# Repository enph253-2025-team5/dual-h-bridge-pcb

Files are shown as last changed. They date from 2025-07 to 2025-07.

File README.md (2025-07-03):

# Dual H-Bridge PCB

Dual h-bridge design with a PWM signal and direction bit for controlling two motors.

Similar to Greg Reid's 2025 h-bridge design, without relying on tripping the overcurrent protection. Instead, this design duplicates the incoming PWM signal, sends one to each of the low side h-bridge MOSFETs, then pulls the gate with the enhanced high side MOSFET low (avoiding shoot-through). 

Based on many factors (motor inertia, gate driver response, optocoupler distortion) the PWM frequency should be limited on the order of 100 Hz.
Intended motor battery configuration of 4S.

**BOM, Schematic, and PCB drawings in the latest release.**

## Images
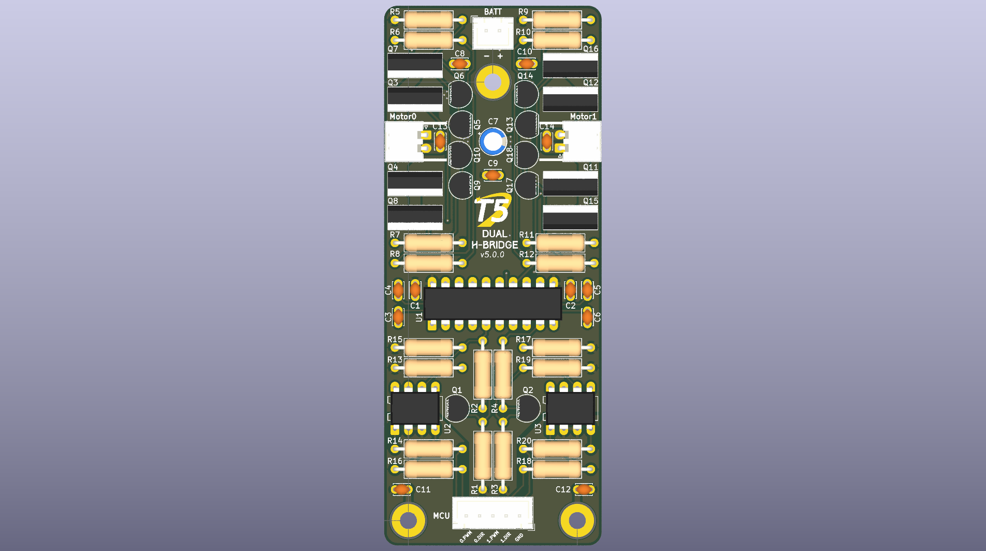
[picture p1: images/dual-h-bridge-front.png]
dual-h-bridge-front

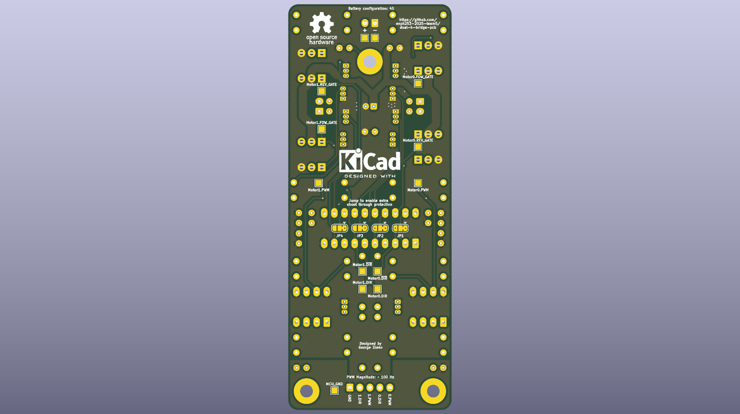
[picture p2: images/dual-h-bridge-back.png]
dual-h-bridge-back

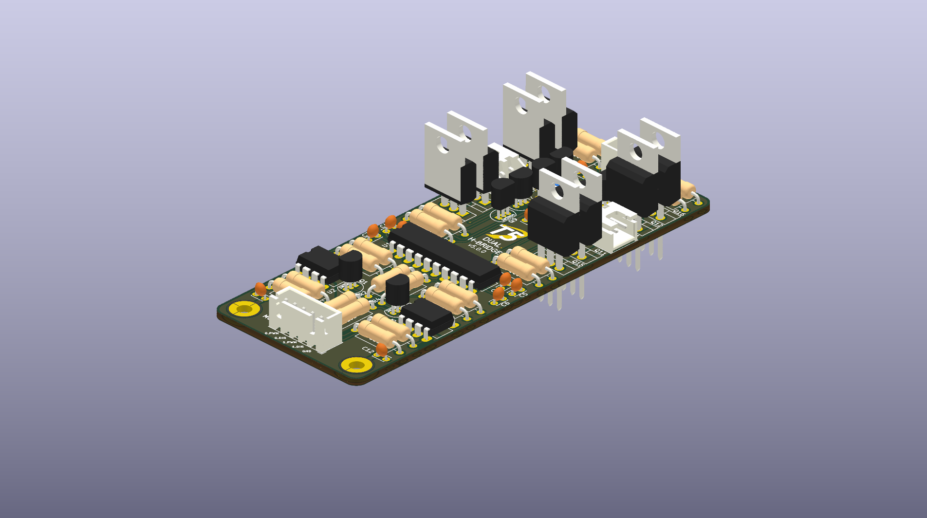
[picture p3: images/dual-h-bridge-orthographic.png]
dual-h-bridge-orthographic


Designed by George Sleen.

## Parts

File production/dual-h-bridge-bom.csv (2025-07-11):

Value | Qty | Reference | Footprint
LT1161 | 1 | U1 | Package_DIP:DIP-20_W7.62mm_LongPads
MCT6 | 2 | U2,U3 | Package_DIP:DIP-8_W7.62mm_LongPads
Motor0 | 1 | J1 | GS_Connectors:JST_XH_S2B-XH-A-1_1x02_P2.50mm_Horizontal
Motor1 | 1 | J3 | GS_Connectors:JST_XH_S2B-XH-A-1_1x02_P2.50mm_Horizontal
BATT | 1 | J4 | Connector_JST:JST_XH_B2B-XH-A_1x02_P2.50mm_Vertical
MCU | 1 | J2 | Connector_JST:JST_XH_B5B-XH-A_1x05_P2.50mm_Vertical
VN2222L | 4 | Q5,Q10,Q13,Q18 | Package_TO_SOT_THT:TO-92_Inline
IRFZ44 | 8 | Q3,Q4,Q7,Q8,Q11,Q12,Q15,Q16 | Package_TO_SOT_THT:TO-220-3_Vertical
2N3904 | 6 | Q1,Q2,Q6,Q9,Q14,Q17 | Package_TO_SOT_THT:TO-92_Inline
47uF | 1 | C7 | Capacitor_THT:CP_Radial_D5.0mm_P2.00mm
10k | 12 | R1,R2,R3,R4,R5,R7,R9,R11,R13,R15,R17,R19 | Resistor_THT:R_Axial_DIN0309_L9.0mm_D3.2mm_P12.70mm_Horizontal
100k | 4 | R6,R8,R10,R12 | Resistor_THT:R_Axial_DIN0309_L9.0mm_D3.2mm_P12.70mm_Horizontal
330R | 4 | R14,R16,R18,R20 | Resistor_THT:R_Axial_DIN0309_L9.0mm_D3.2mm_P12.70mm_Horizontal
100nF | 9 | C1,C2,C8,C9,C10,C11,C12,C13,C14 | Capacitor_THT:C_Disc_D3.0mm_W2.0mm_P2.50mm
10nF | 4 | C3,C4,C5,C6 | Capacitor_THT:C_Disc_D3.0mm_W2.0mm_P2.50mm

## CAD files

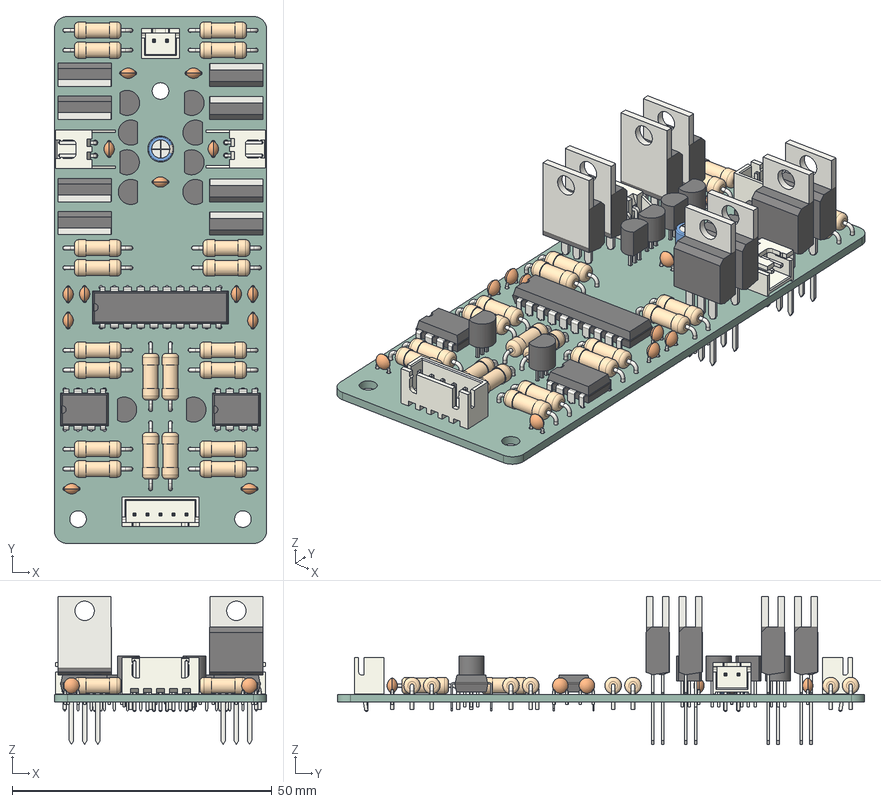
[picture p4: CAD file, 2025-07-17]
3d-model/dual-h-bridge.step
40.9 x 101.5 x 28.5 mm
TO-92_Inline x 10
R_Axial_DIN0309_L9.0mm_D3.2mm_P12.70mm_Horizontal x 20
C_Disc_D3.0mm_W2.0mm_P2.50mm x 13
CP_Radial_D5.0mm_P2.00mm
TO-220-3_Vertical x 8
JST_XH_B2B-XH-A_1x02_P2.50mm_Vertical
JST_XH_S2B-XH-A-1_1x02_P2.50mm_Horizontal x 2
DIP-8_W7.62mm x 2
JST_XH_B5B-XH-A_1x05_P2.50mm_Vertical
DIP-20_W7.62mm
dual-h-bridge_PCB

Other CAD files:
drawings/dual-h-bridge.step
prod/motor-controller.step
drawings/.step

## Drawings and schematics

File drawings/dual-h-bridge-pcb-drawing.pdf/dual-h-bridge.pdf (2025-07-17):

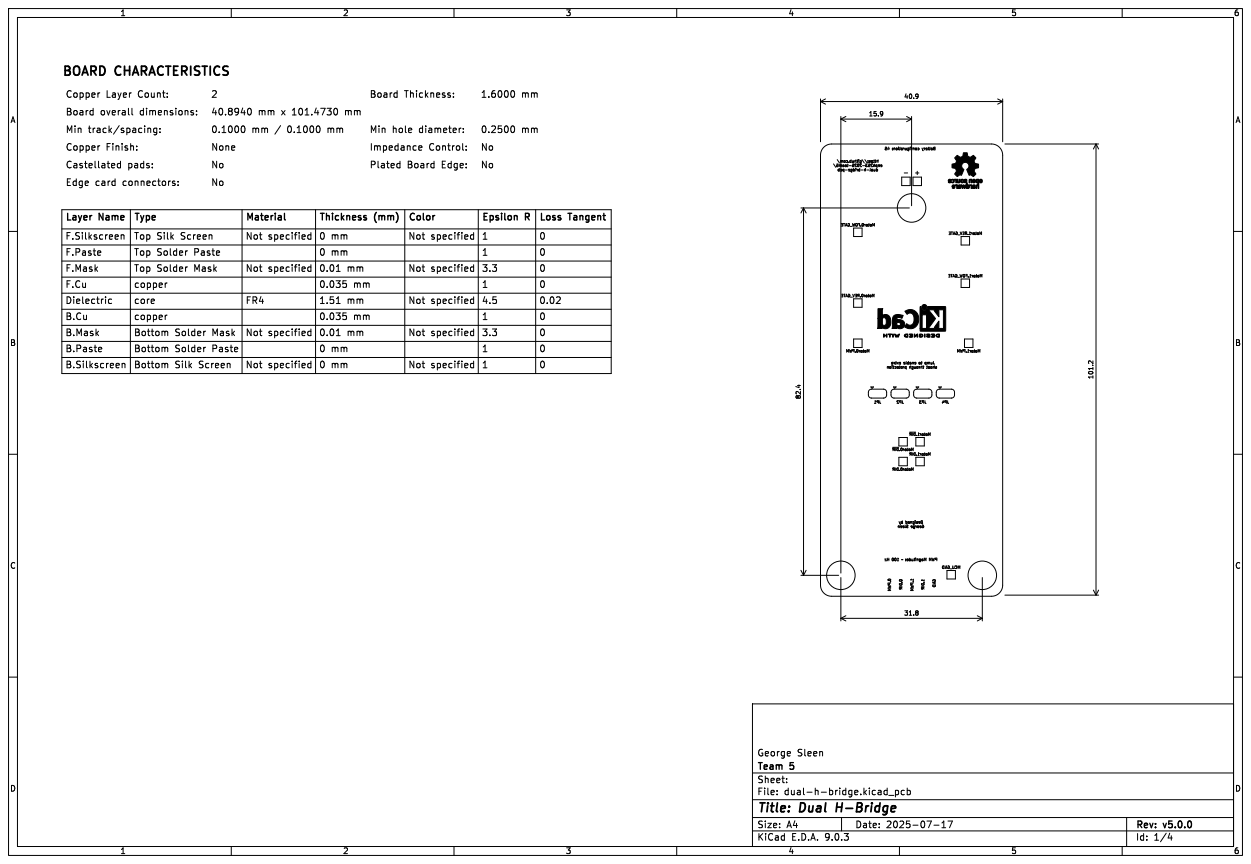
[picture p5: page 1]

Layer Name Copper Finish: | Thickness (mm) | Not specified | 3.3 Plated Board Edge: 1.51 mm | 0

F.Silkscreen F.Paste | | | | Material | 0 mm | Not specified | 4.5 Not specified | Loss Tangent Not specified 0

Top Silk Screen | | 0 mm | | 1

0.035 mm | | | 0 Bottom Silk Screen 0

core B.Silkscreen | | 0.035 mm

0 Not specified

Bottom Solder Paste

File: dual-h-bridge.kicad_pcb Sheet: Team 5 George Sleen

Id: 1/4 Title: Dual H-Bridge

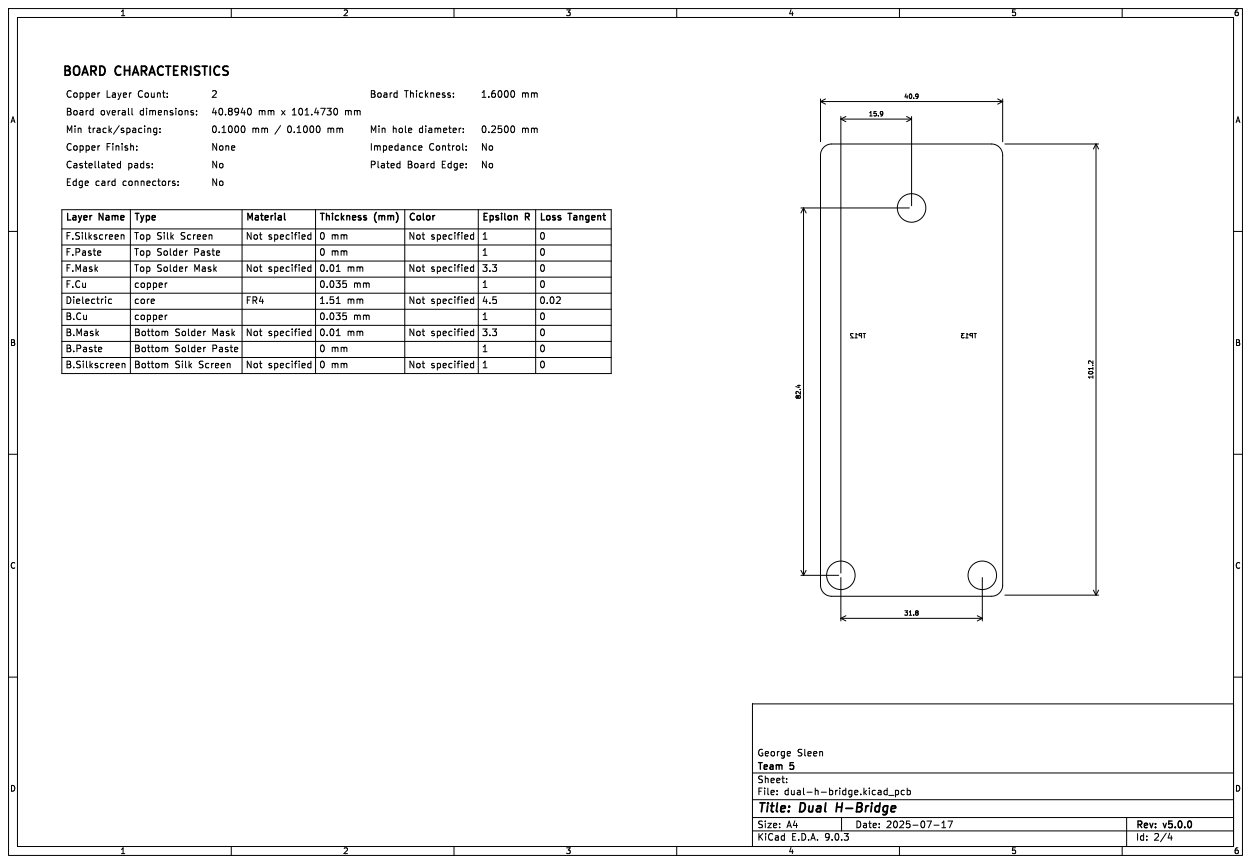
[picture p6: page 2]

Layer Name Copper Finish: | Thickness (mm) mm | Not specified Board Edge: 1.51 | 3.3 Plated | 0

F.Silkscreen F.Paste | | | | Material | 0 mm | Not specified | | Loss Tangent Not specified 0

Top Silk Screen | | 0 mm | | | 1

Screen | | 0.035 mm | | | 0 Bottom Silk 0

core B.Silkscreen | | 0.035 mm

0 Not specified

File: dual-h-bridge.kicad_pcb Sheet: Team 5 George Sleen

Id: 2/4 Title: Dual H-Bridge

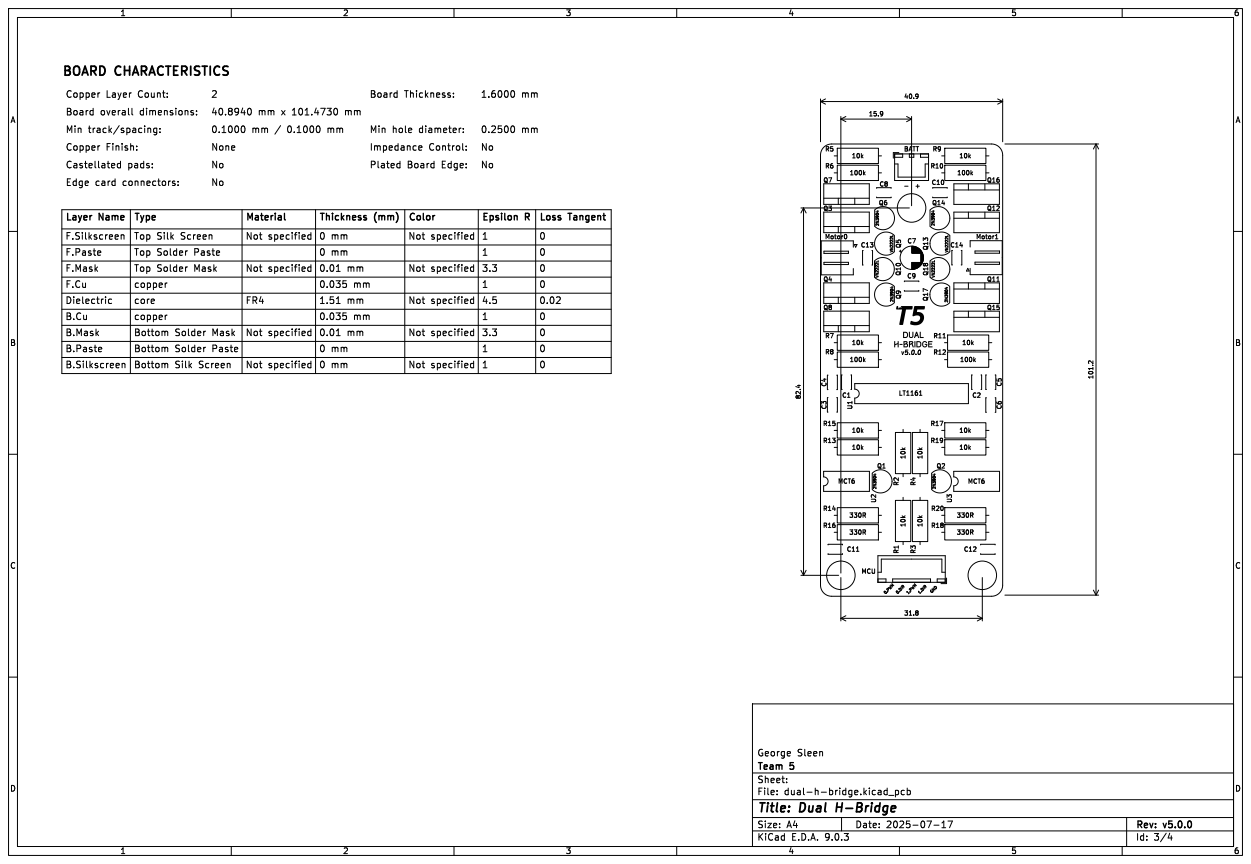
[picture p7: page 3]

Layer Name Copper Finish: | | Thickness (mm) | Not specified | 3.3 Plated Board Edge: 1.51 mm Epsilon R | 0

F.Silkscreen F.Paste | | | | Material | 0 mm | Not specified | 4.5 Not specified | Loss Tangent Not specified 0
0 mm 0.035 mm | Not specified F.Mask | | 0 Bottom Silk Screen 0

Top Silk Screen | 0 mm | | 1

core B.Silkscreen | | | | 0.035 mm

FR4 | | | | 0.02
0.01 mm | | | 0 Not specified

Bottom Solder Paste | | | | | | 1

File: dual-h-bridge.kicad_pcb Sheet: Team 5 George Sleen

Id: 3/4 Title: Dual H-Bridge

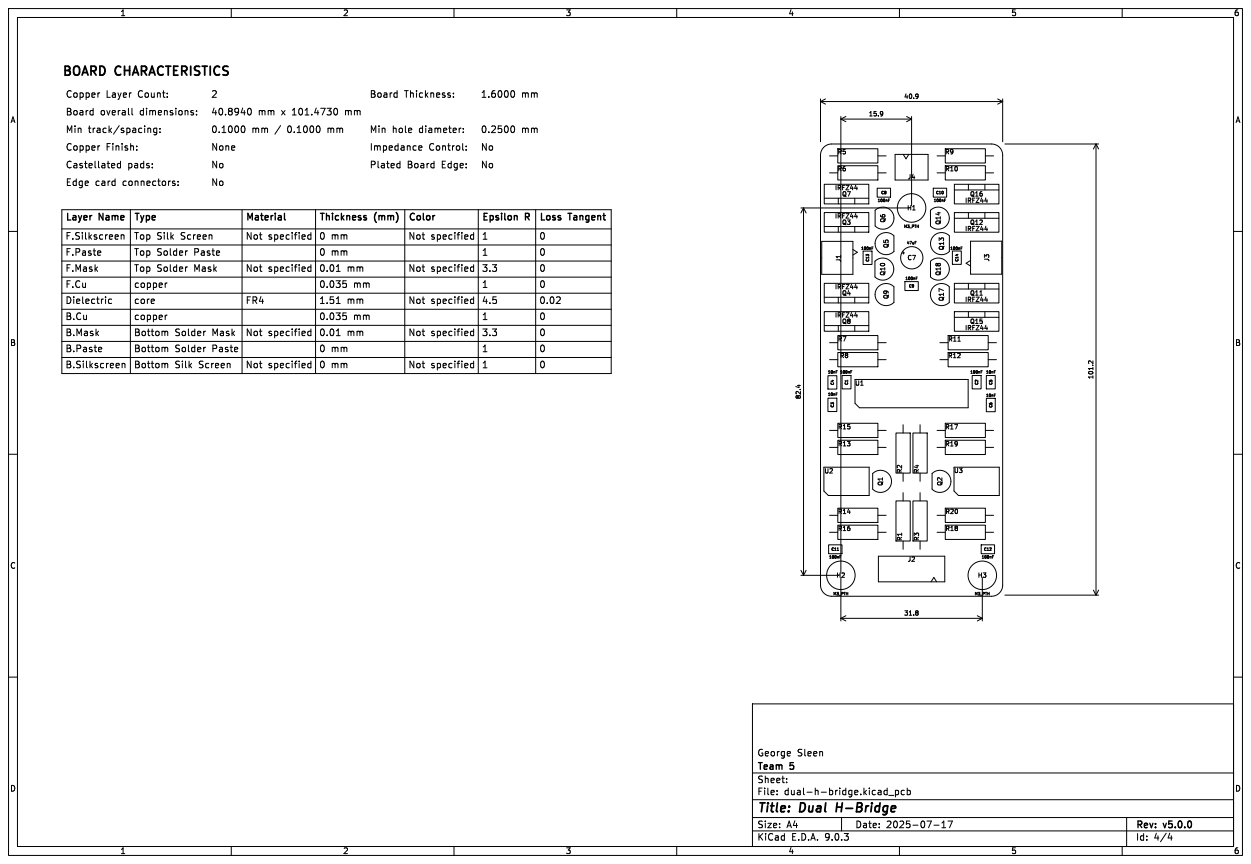
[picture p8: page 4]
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

Top Silk Screen | 0 mm | | 1

0.035 mm | | | 0 Bottom Silk Screen 0

0 Not specified

Bottom Solder Paste

Id: 4/4 Title: Dual H-Bridge

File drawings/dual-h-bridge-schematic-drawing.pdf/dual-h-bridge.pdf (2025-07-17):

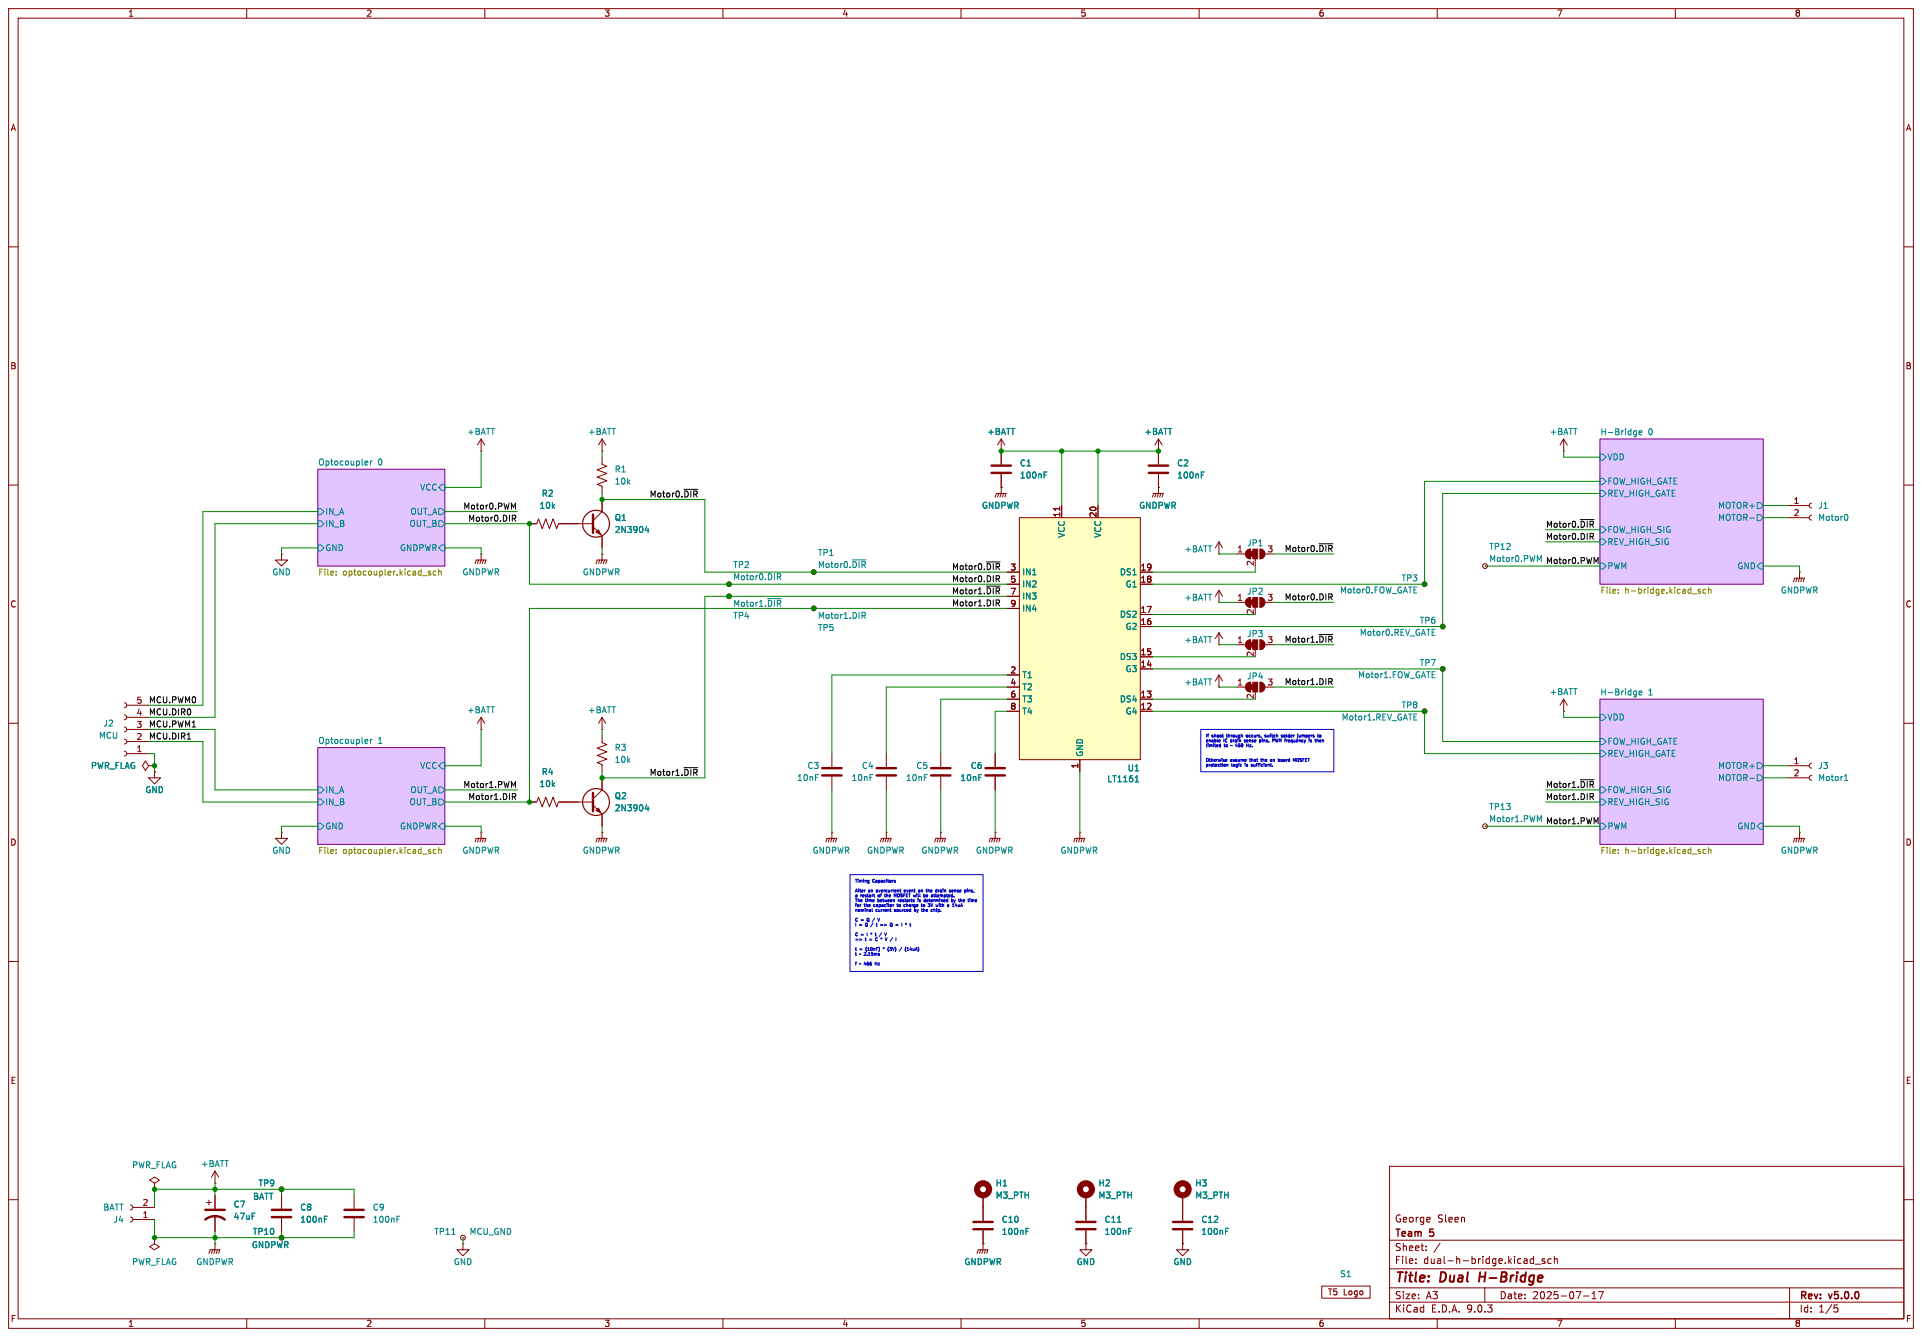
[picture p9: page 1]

Id: 1/5 Title: Dual H-Bridge

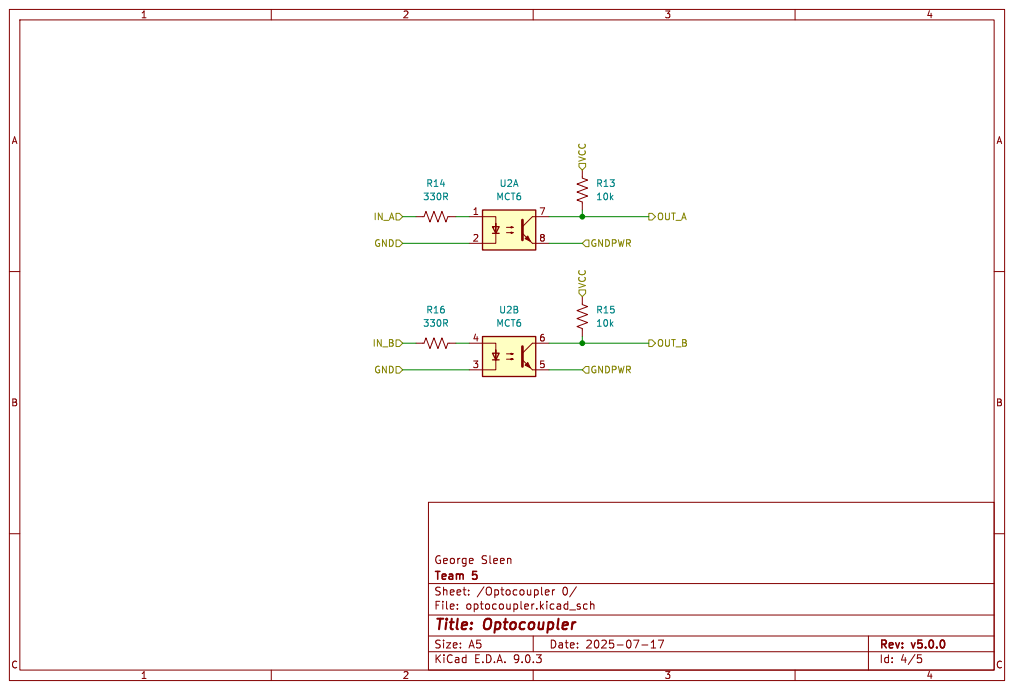
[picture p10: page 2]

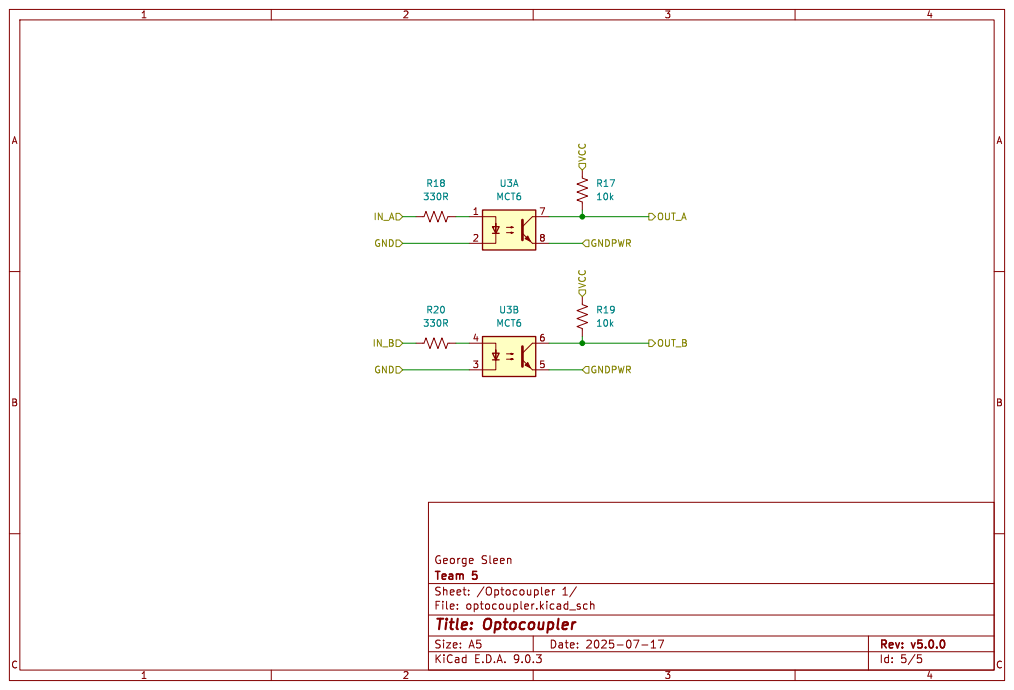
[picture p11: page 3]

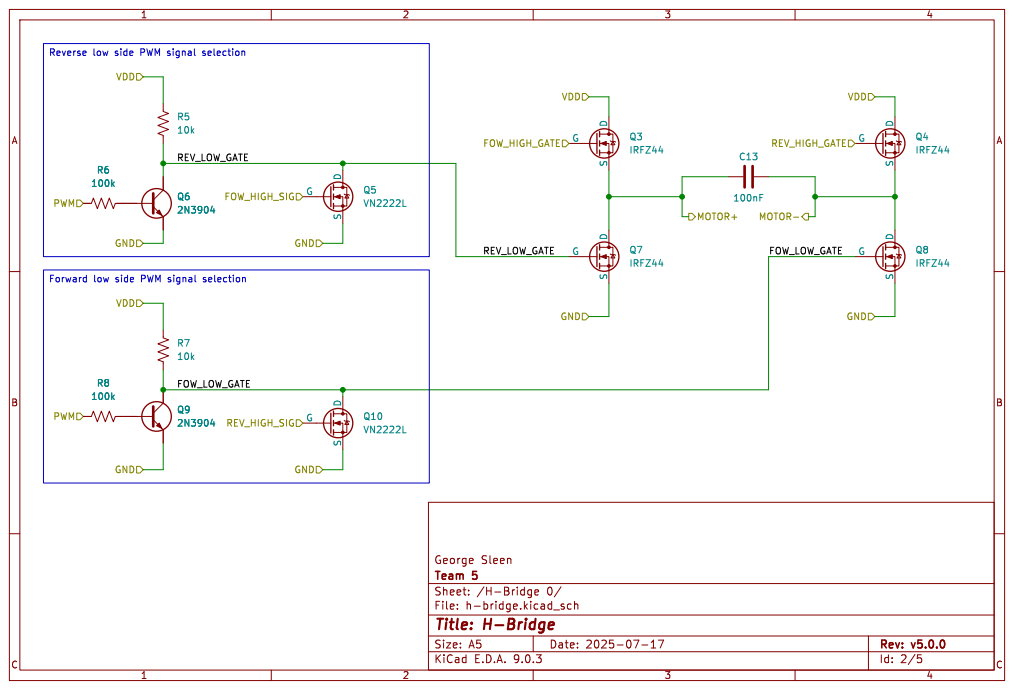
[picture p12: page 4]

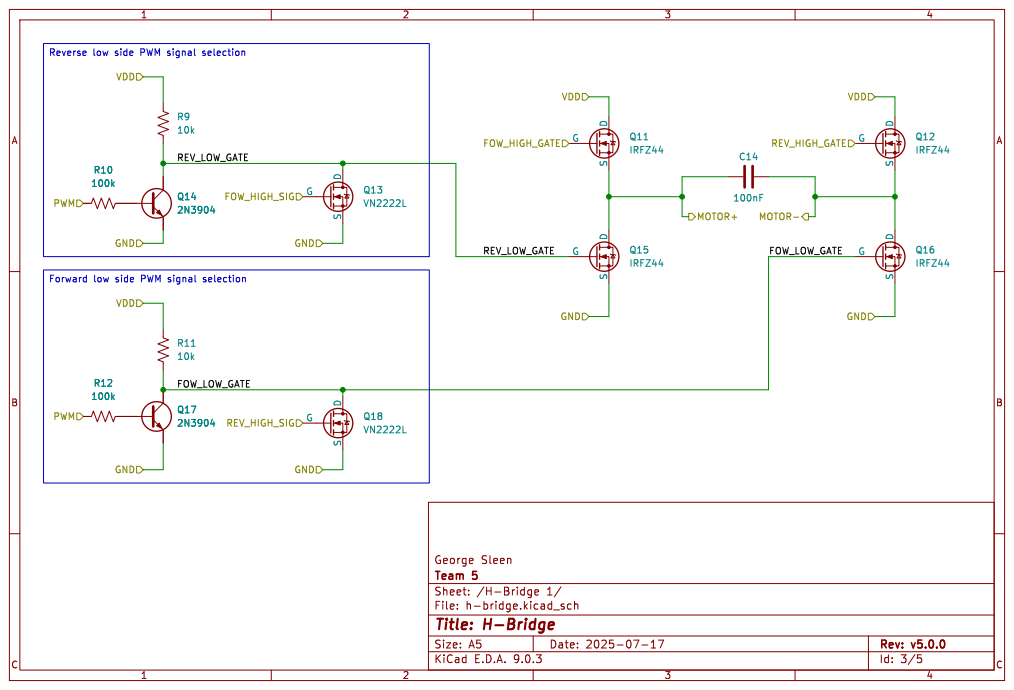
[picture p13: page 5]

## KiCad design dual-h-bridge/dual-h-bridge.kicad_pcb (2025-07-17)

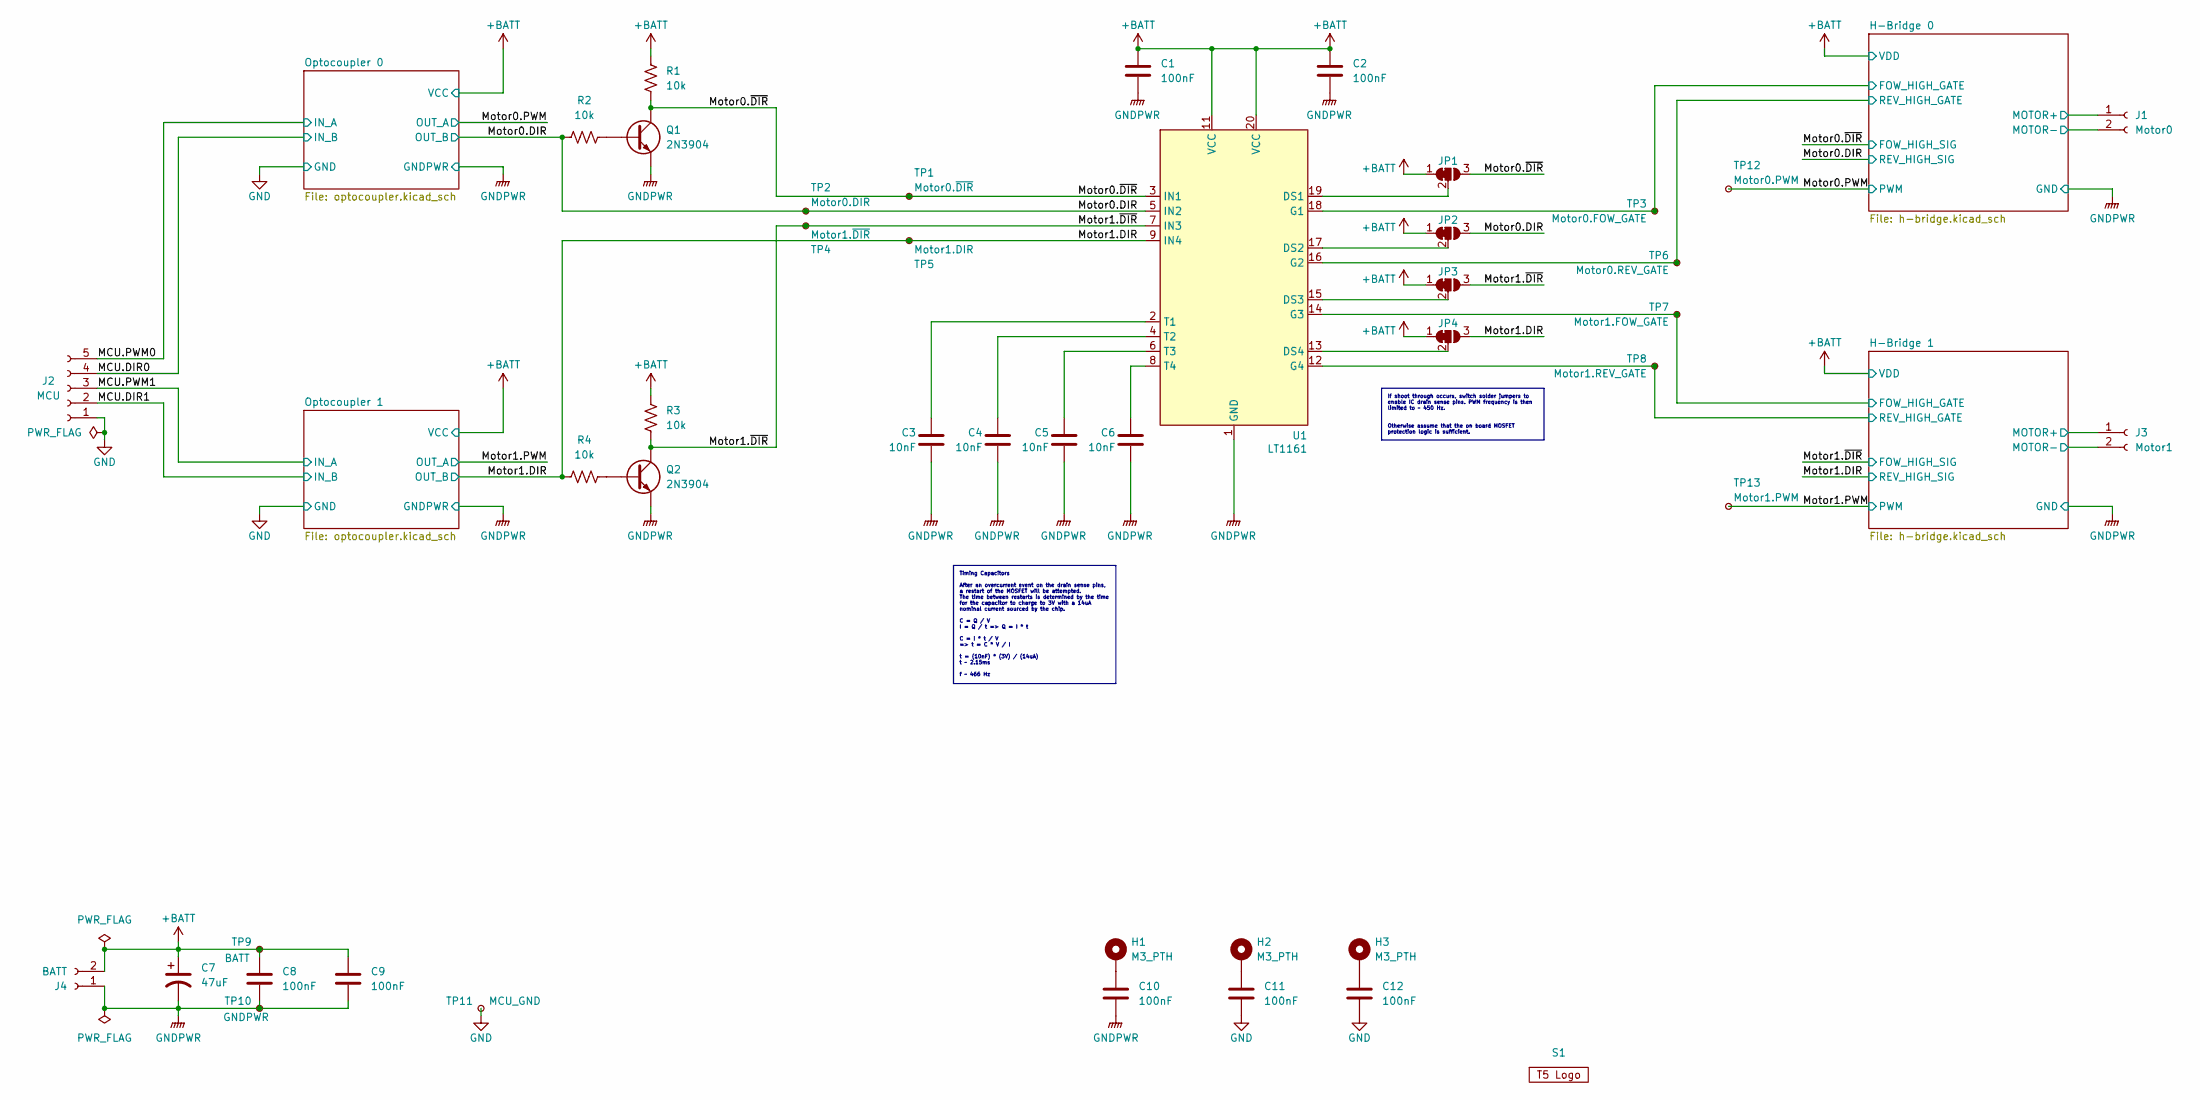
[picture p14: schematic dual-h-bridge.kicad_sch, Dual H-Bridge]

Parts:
C1, C2, C8, C9, C10, C11, C12: 100nF; C_Disc_D3.0mm_W2.0mm_P2.50mm
C3, C4, C5, C6: 10nF; C_Disc_D3.0mm_W2.0mm_P2.50mm
C7: 47uF; CP_Radial_D5.0mm_P2.00mm
H1, H2, H3: M3_PTH; MountingHole_3.2mm_M3_Pad
J1: Motor0; JST_XH_S2B-XH-A-1_1x02_P2.50mm_Horizontal
J2: MCU; JST_XH_B5B-XH-A_1x05_P2.50mm_Vertical
J3: Motor1; JST_XH_S2B-XH-A-1_1x02_P2.50mm_Horizontal
J4: BATT; JST_XH_B2B-XH-A_1x02_P2.50mm_Vertical
JP1: Motor0_FOW; SolderJumper-3_P1.3mm_Bridged12_RoundedPad1.0x1.5mm
JP2: MOTOR0_REV; SolderJumper-3_P1.3mm_Bridged12_RoundedPad1.0x1.5mm
JP3: MOTOR1_FOW; SolderJumper-3_P1.3mm_Bridged12_RoundedPad1.0x1.5mm
JP4: MOTOR1_REV; SolderJumper-3_P1.3mm_Bridged12_RoundedPad1.0x1.5mm
Q1, Q2: 2N3904; TO-92_Inline
R1, R2, R3, R4: 10k; R_Axial_DIN0309_L9.0mm_D3.2mm_P12.70mm_Horizontal
S1: Logo; ENPH253_Logo_Small
TP1: Motor0.~{DIR}; TestPoint_Pad_1.5x1.5mm
TP2: Motor0.DIR; TestPoint_Pad_1.5x1.5mm
TP3: Motor0.FOW_GATE; TestPoint_Pad_1.5x1.5mm
TP4: Motor1.~{DIR}; TestPoint_Pad_1.5x1.5mm
TP5: Motor1.DIR; TestPoint_Pad_1.5x1.5mm
TP6: Motor0.REV_GATE; TestPoint_Pad_1.5x1.5mm
TP7: Motor1.FOW_GATE; TestPoint_Pad_1.5x1.5mm
TP8: Motor1.REV_GATE; TestPoint_Pad_1.5x1.5mm
TP9: BATT; TestPoint_Pad_1.5x1.5mm
TP10: GNDPWR; TestPoint_Pad_1.5x1.5mm
TP11: MCU_GND; TestPoint_Pad_1.5x1.5mm
TP12: Motor0.PWM; TestPoint_Pad_1.5x1.5mm
TP13: Motor1.PWM; TestPoint_Pad_1.5x1.5mm
U1: LT1161; DIP-20_W7.62mm_LongPads

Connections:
+BATT: C1.1, C2.1, C7.1, C8.1, C9.1, J4.2, JP1.1 (A), JP2.1 (A), JP3.1 (A), JP4.1 (A), R1.1, R3.1, TP9.1, U1.11 (VCC), U1.20 (VCC); also elsewhere on the board
/H-Bridge 0/FOW_HIGH_GATE: TP3.1, U1.18 (G1); also elsewhere on the board
/H-Bridge 0/MOTOR+: J1.1; also elsewhere on the board
/H-Bridge 0/MOTOR-: J1.2; also elsewhere on the board
/H-Bridge 0/REV_HIGH_GATE: TP6.1, U1.16 (G2); also elsewhere on the board
/H-Bridge 1/FOW_HIGH_GATE: TP7.1, U1.14 (G3); also elsewhere on the board
/H-Bridge 1/MOTOR+: J3.1; also elsewhere on the board
/H-Bridge 1/MOTOR-: J3.2; also elsewhere on the board
/H-Bridge 1/REV_HIGH_GATE: TP8.1, U1.12 (G4); also elsewhere on the board
/MCU.DIR0: J2.4; also elsewhere on the board
/MCU.DIR1: J2.2; also elsewhere on the board
/MCU.PWM0: J2.5; also elsewhere on the board
/MCU.PWM1: J2.3; also elsewhere on the board
/Motor0.DIR: JP2.3 (B), R2.1, TP2.1, U1.5 (IN2); also elsewhere on the board
/Motor0.PWM: TP12.1; also elsewhere on the board
/Motor0.~DIR: JP1.3 (B), Q1.3 (C), R1.2, TP1.1, U1.3 (IN1); also elsewhere on the board
/Motor1.DIR: JP4.3 (B), R4.1, TP5.1, U1.9 (IN4); also elsewhere on the board
/Motor1.PWM: TP13.1; also elsewhere on the board
/Motor1.~DIR: JP3.3 (B), Q2.3 (C), R3.2, TP4.1, U1.7 (IN3); also elsewhere on the board
GND: C11.2, C12.2, J2.1, TP11.1; also elsewhere on the board
GNDPWR: C1.2, C2.2, C3.2, C4.2, C5.2, C6.2, C7.2, C8.2, C9.2, C10.2, J4.1, Q1.1 (E), Q2.1 (E), TP10.1, U1.1 (GND), U1.10 (GND); also elsewhere on the board
unnamed: C10.1, H1.1
unnamed: C11.1, H2.1
unnamed: C12.1, H3.1
unnamed: JP1.2 (C), U1.19 (DS1)
unnamed: JP2.2 (C), U1.17 (DS2)
unnamed: JP3.2 (C), U1.15 (DS3)
unnamed: JP4.2 (C), U1.13 (DS4)
unnamed: Q1.2 (B), R2.2
unnamed: Q2.2 (B), R4.2
unnamed: C3.1, U1.2 (T1)
unnamed: C4.1, U1.4 (T2)
unnamed: C5.1, U1.6 (T3)
unnamed: C6.1, U1.8 (T4)

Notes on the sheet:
If shoot through occurs, switch solder jumpers to enable IC drain sense pins. PWM frequency is then limited to ~ 450 Hz. Otherwise assume that the on board MOSFET protection logic is sufficient.
Timing Capacitors After an overcurrent event on the drain sense pins, a restart of the MOSFET will be attempted. The time between restarts is determined by the time for the capacitor to charge to 3V with a 14uA nominal current sourced by the chip. C = Q / V I = Q / t => Q = I * t C = I * t / V => t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

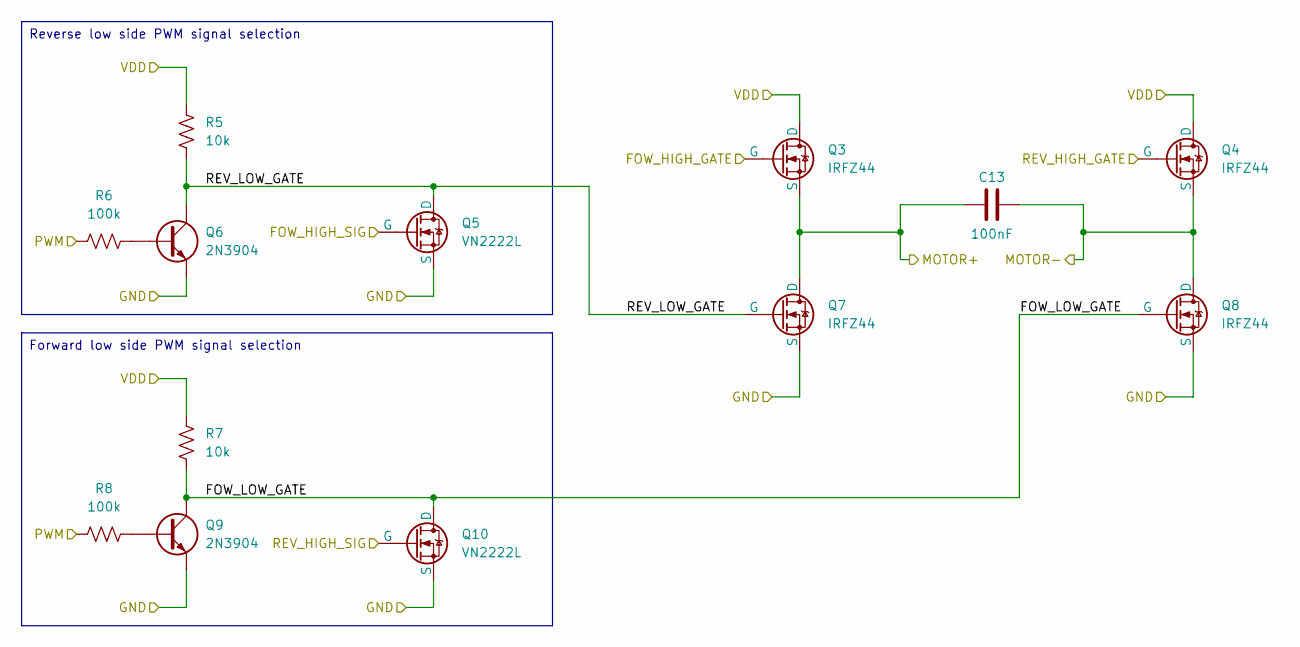
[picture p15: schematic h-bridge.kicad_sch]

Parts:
C13: 100nF; C_Disc_D3.0mm_W2.0mm_P2.50mm
Q3, Q4, Q7, Q8: IRFZ44; TO-220-3_Vertical
Q5, Q10: VN2222L; TO-92_Inline
Q6, Q9: 2N3904; TO-92_Inline
R5, R7: 10k; R_Axial_DIN0309_L9.0mm_D3.2mm_P12.70mm_Horizontal
R6, R8: 100k; R_Axial_DIN0309_L9.0mm_D3.2mm_P12.70mm_Horizontal

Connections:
+BATT: Q3.2 (D), Q4.2 (D), R5.1, R7.1; also elsewhere on the board
/H-Bridge 0/FOW_HIGH_GATE: Q3.1 (G); also elsewhere on the board
/H-Bridge 0/FOW_LOW_GATE: Q8.1 (G), Q9.3 (C), Q10.3 (D), R7.2
/H-Bridge 0/MOTOR+: C13.1, Q3.3 (S), Q7.2 (D); also elsewhere on the board
/H-Bridge 0/MOTOR-: C13.2, Q4.3 (S), Q8.2 (D); also elsewhere on the board
/H-Bridge 0/REV_HIGH_GATE: Q4.1 (G); also elsewhere on the board
/H-Bridge 0/REV_LOW_GATE: Q5.3 (D), Q6.3 (C), Q7.1 (G), R5.2
/Motor0.DIR: Q10.2 (G); also elsewhere on the board
/Motor0.PWM: R6.1, R8.1; also elsewhere on the board
/Motor0.~DIR: Q5.2 (G); also elsewhere on the board
GNDPWR: Q5.1 (S), Q6.1 (E), Q7.3 (S), Q8.3 (S), Q9.1 (E), Q10.1 (S); also elsewhere on the board
unnamed: Q6.2 (B), R6.2
unnamed: Q9.2 (B), R8.2

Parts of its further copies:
C14: 100nF; C_Disc_D3.0mm_W2.0mm_P2.50mm
Q11, Q12, Q15, Q16: IRFZ44; TO-220-3_Vertical
Q13, Q18: VN2222L; TO-92_Inline
Q14, Q17: 2N3904; TO-92_Inline
R9, R11: 10k; R_Axial_DIN0309_L9.0mm_D3.2mm_P12.70mm_Horizontal
R10, R12: 100k; R_Axial_DIN0309_L9.0mm_D3.2mm_P12.70mm_Horizontal

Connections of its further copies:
+BATT: Q11.2 (D), Q12.2 (D), R9.1, R11.1; also elsewhere on the board
/H-Bridge 1/FOW_HIGH_GATE: Q11.1 (G); also elsewhere on the board
/H-Bridge 1/FOW_LOW_GATE: Q16.1 (G), Q17.3 (C), Q18.3 (D), R11.2
/H-Bridge 1/MOTOR+: C14.1, Q11.3 (S), Q15.2 (D); also elsewhere on the board
/H-Bridge 1/MOTOR-: C14.2, Q12.3 (S), Q16.2 (D); also elsewhere on the board
/H-Bridge 1/REV_HIGH_GATE: Q12.1 (G); also elsewhere on the board
/H-Bridge 1/REV_LOW_GATE: Q13.3 (D), Q14.3 (C), Q15.1 (G), R9.2
/Motor1.DIR: Q18.2 (G); also elsewhere on the board
/Motor1.PWM: R10.1, R12.1; also elsewhere on the board
/Motor1.~DIR: Q13.2 (G); also elsewhere on the board
GNDPWR: Q13.1 (S), Q14.1 (E), Q15.3 (S), Q16.3 (S), Q17.1 (E), Q18.1 (S); also elsewhere on the board
unnamed: Q14.2 (B), R10.2
unnamed: Q17.2 (B), R12.2

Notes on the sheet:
Reverse low side PWM signal selection
Forward low side PWM signal selection

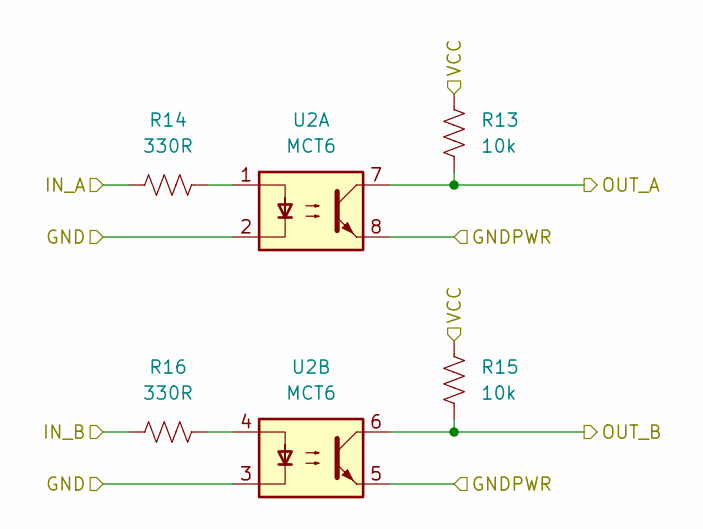
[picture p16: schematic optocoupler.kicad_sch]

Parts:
R13, R15: 10k; R_Axial_DIN0309_L9.0mm_D3.2mm_P12.70mm_Horizontal
R14, R16: 330R; R_Axial_DIN0309_L9.0mm_D3.2mm_P12.70mm_Horizontal
U2: MCT6; DIP-8_W7.62mm_LongPads

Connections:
+BATT: R13.2, R15.2; also elsewhere on the board
/MCU.DIR0: R16.1; also elsewhere on the board
/MCU.PWM0: R14.1; also elsewhere on the board
/Motor0.DIR: R15.1, U2.6; also elsewhere on the board
/Motor0.PWM: R13.1, U2.7; also elsewhere on the board
GND: U2.2, U2.3; also elsewhere on the board
GNDPWR: U2.5, U2.8; also elsewhere on the board
unnamed: R14.2, U2.1
unnamed: R16.2, U2.4

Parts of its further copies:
R17, R19: 10k; R_Axial_DIN0309_L9.0mm_D3.2mm_P12.70mm_Horizontal
R18, R20: 330R; R_Axial_DIN0309_L9.0mm_D3.2mm_P12.70mm_Horizontal
U3: MCT6; DIP-8_W7.62mm_LongPads

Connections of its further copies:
+BATT: R17.2, R19.2; also elsewhere on the board
/MCU.DIR1: R20.1; also elsewhere on the board
/MCU.PWM1: R18.1; also elsewhere on the board
/Motor1.DIR: R19.1, U3.6; also elsewhere on the board
/Motor1.PWM: R17.1, U3.7; also elsewhere on the board
GND: U3.2, U3.3; also elsewhere on the board
GNDPWR: U3.5, U3.8; also elsewhere on the board
unnamed: R18.2, U3.1
unnamed: R20.2, U3.4

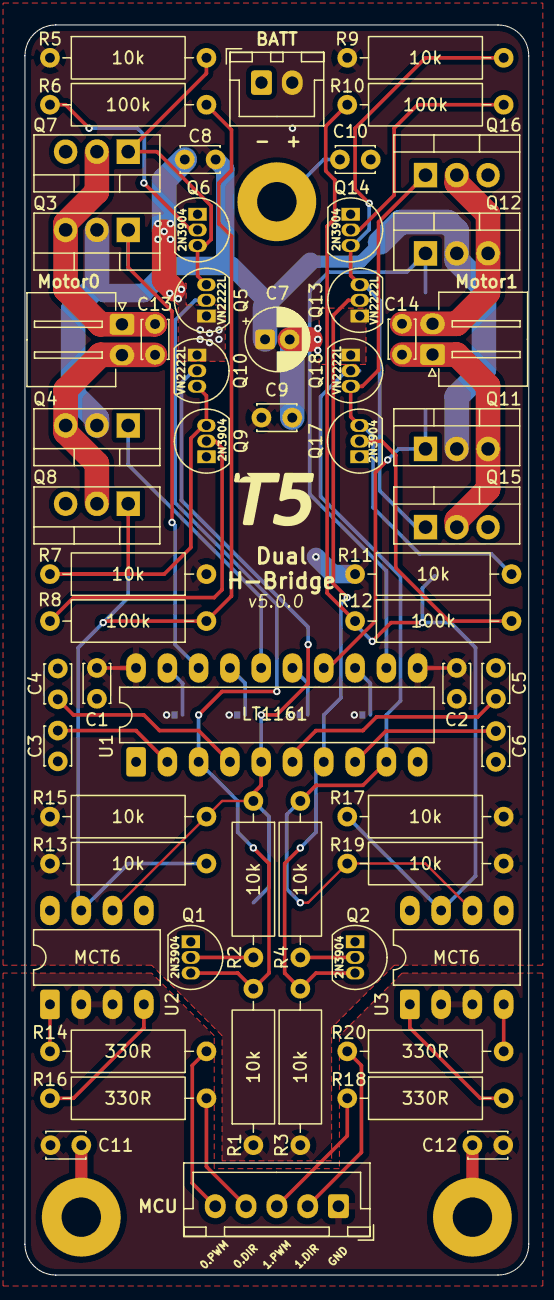
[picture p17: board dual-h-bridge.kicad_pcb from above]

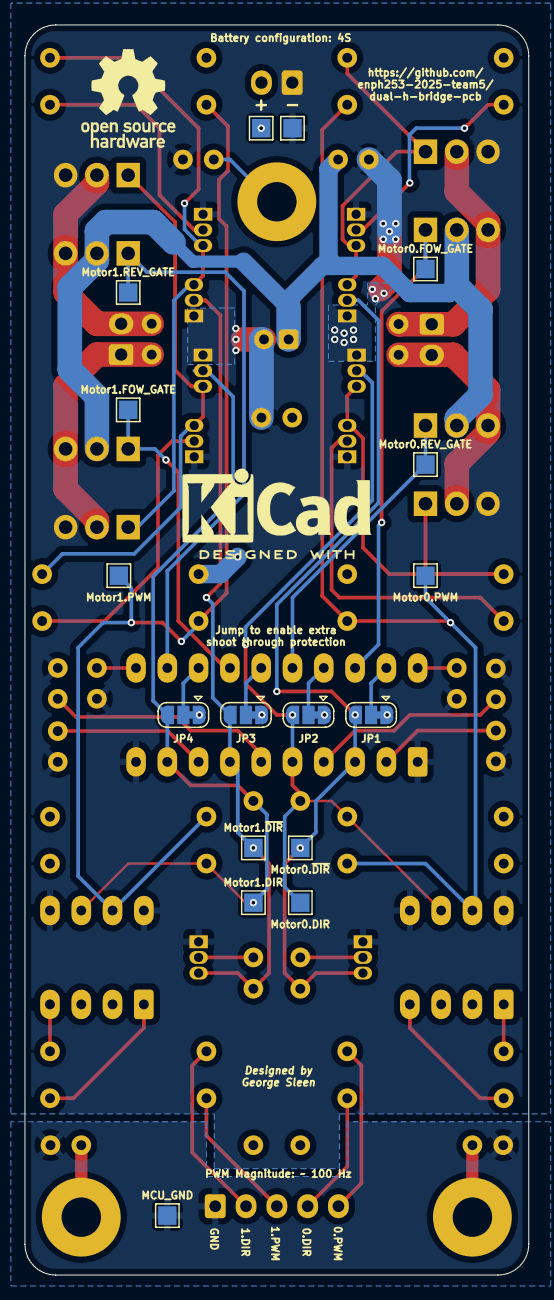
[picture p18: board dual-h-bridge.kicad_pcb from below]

Board: 2 copper layers, 40.9 x 101.5 mm, 80 parts (17 on the bottom side), 46 nets.

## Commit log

2025-05-16 Create project structure
    [H-Bridge.kicad_pcb, H-Bridge.kicad_sch]
2025-06-06 Change project name
    [H-Bridge.kicad_sch, h-bridge.kicad_sch, motor-controller.kicad_pcb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]
2025-06-06 Create H-Bridge schematic
    [h-bridge.kicad_sch, motor-controller.kicad_sch]
2025-06-06 Finish optocoupler and gate-driver
    [h-bridge.kicad_sch, motor-controller.kicad_sch, optocoupler.kicad_sch]
2025-06-06 Finish H-Bridge schematic
    [h-bridge.kicad_sch, motor-controller.kicad_sch, optocoupler.kicad_sch]
2025-06-15 Change h-bridge design to newer version
    [h-bridge.kicad_sch, motor-controller.kicad_pcb, motor-controller.kicad_sch]
2025-06-15 Fix some ERC issues
    [h-bridge.kicad_sch, motor-controller.kicad_sch, optocoupler.kicad_sch]
2025-06-19 Update PWM signal selection to avoid an accidental resistor divider
    [h-bridge.kicad_sch, motor-controller-BOM.csv, motor-controller.kicad_pcb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]
2025-06-19 Finish layout
    [motor-controller.kicad_pcb, motor-controller.kicad_sch, optocoupler.kicad_sch]
2025-06-20 Generate schematic pdf
    [motor-controller.kicad_pcb, motor-controller.kicad_sch, motor-controller.step]
2025-06-20 Add engineering drawings for the PCB
    [motor-controller.kicad_pcb]
2025-06-20 Change name and produce production outputs
    [.step, dual-h-bridge-bom.csv, dual-h-bridge.kicad_pcb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]
2025-06-20 Fix some production outputs
    [dual-h-bridge-bom.csv, dual-h-bridge.step]
2025-06-22 minor changes to back silkscreen
    [dual-h-bridge-bom.csv, dual-h-bridge.kicad_pcb, dual-h-bridge.step]
2025-06-22 Update README.md to reflect most current release
2025-07-02 Update to right angle motor connectors
    [dual-h-bridge-bom.csv, dual-h-bridge.kicad_pcb, dual-h-bridge.kicad_sch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]
2025-07-05 Fix potentially inverted H-Bridge direction bit
    [dual-h-bridge-bom.csv, dual-h-bridge.kicad_pcb, dual-h-bridge.kicad_sch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]
2025-07-06 Update silkscreen
    [dual-h-bridge.kicad_pcb, dual-h-bridge.step]
2025-07-09 Fix optocoupler hardware issue
    [dual-h-bridge.kicad_pcb, dual-h-bridge.kicad_sch, h-bridge.kicad_sch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]
2025-07-09 Generate production outputs
    [dual-h-bridge.step]
2025-07-10 Some small updates
    [dual-h-bridge-3d-model_v3.0.0.step, dual-h-bridge-bom_v3.0.0.csv, dual-h-bridge.kicad_pcb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]
2025-07-10 More changes
    [dual-h-bridge.kicad_sch, h-bridge.kicad_sch, optocoupler.kicad_sch]
2025-07-11 Fix all hardware issues and generate final release source files
    [dual-h-bridge-3d-model_v3.0.0.step, dual-h-bridge-bom_v3.0.0.csv, dual-h-bridge.kicad_pcb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]
2025-07-11 Generate release package with all hardware issues fixed
    [dual-h-bridge-bom.csv, dual-h-bridge.step]
2025-07-17 Fix source and drain being swapped on small signal mosfet
    [dual-h-bridge.kicad_pcb, dual-h-bridge.kicad_sch, h-bridge.kicad_sch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]
2025-07-17 Generate v5.0.0 production files
    [dual-h-bridge.step]
